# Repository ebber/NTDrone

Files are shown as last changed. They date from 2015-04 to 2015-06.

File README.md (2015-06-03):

# NTDrone
NT Drone DE
This is code to stabilize and control a drone.
3D printing design files coming soon!

Connections:
Pin	Connect to
2	MPU Interupt Pin
6	Motor C Signal Cable
9	Motor D Signal Cable
10	Motor A Signal Cable
11	Motor B Signal Cable
13	LED (blinks error codes)

A4	MPU SDA
A5 	MPU SCA

Using:
Motors/ESC: BEC ESC 10A
input voltage: {6, 7.5, 9, 12 (short periods of time)}

low signal: 900 uS
High signal: 2000uS

Arming sequence:
unneeded 

/*
Previous
Motors/ESC: HobbyKing RedBrick ESC 10A
input voltage: {6, 7.5, 9, 12 (short periods of time)}

low signal: 1000 uS
High signal: 2000uS

Arming sequence:
1000uS
delay(500);
2000uS
//armed
*/

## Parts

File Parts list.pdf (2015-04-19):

| Parts | weight (g) | cost | quantity | total part cost | total part weight (g | overall drone cost | total weight (g)
Motor | 2205C 1400Kv Brushless motor (http://hobbyking.com/hobbyking/store/__7520__2205C_1400Kv_Brushless_motor.html) | 28.00 | $11.75 | 4 | $47.00 | 112.00 | $235.19 | 1,198.43
Propellers | APC style propeller 10x5-E (http://www.hobbyking.com/hobbyking/store/__5440__APC_style_propeller_10x5_E.html) | 35.00 | $0.75 | 4 | $3.00 | 140.00
Speed Controler | HobbyKing Red Brick 10A ESC (http://hobbyking.com/hobbyking/store/__18002__HobbyKing_Red_Brick_10A_ESC.html) | 18.00 | $6.55 | 4 | $26.20 | 72.00

Sensors
acceleramoter | MPU 6050 (http://www.gearbest.com/development-boards/pp_22492.html?currency=USD) | 1.10 | $7.68 | 1 | $7.68 | 1.10
Battery | Turnigy 2200mAh 3S 20C Lipo Pack | 188.00 | $8.76 | 1 | $8.76 | 188.00
Power Distributer | Hobby King Quadcopter distributer (http://hobbyking.com/hobbyking/store/__28255__Hobby_King_Quadcopter_Power_Distribution_Board_USA_Warehouse_.html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) | 27.30 | $4.19 | 1 | | 27.30
ardunio boards | Arduino Uno | 25.00 | $22.63 | 1 | $22.63 | 25.00

Shields
Wireless - XBee | XBee 1mW Trace Antenna - Series 1 (802.15.4) (https://www.sparkfun.com/products/11215) | 5.00 | $24.95 | 1 | $24.95 | 5.00
XBee Shield | XBEE Shield | 37.00 | $10.00 | 1 | $10.00 | 37.00
Bluetooth | SparkFun Bluetooth Mate Gold (https://www.sparkfun.com/products/12580) | | $34.95 | 0 | $0.00

misc.
| 3.5mm bullet male connectors (10pc) (http://www.amazon.com/gp/product/B00J80EP8G/ref=oh_aui_detailpage_o01_s00?ie=UTF8&psc=1) | | 8 | $9.95
| USB B to A (for power) | $5.09 | 1 | $5.09
Airframe | bowel design | 591.03 | 1 | 591.03

Remote Control
Wireless - XBee | XBee 1mW Trace Antenna - Series 1 (802.15.4) (https://www.sparkfun.com/products/11215) | 5.00 | $24.95 | 1 | $24.95
XBee Shield | XBEE Shield | 37.00 | $10.00 | 1 | $10.00
ardunio boards | Arduino Uno | 25.00 | $22.63 | 1 | $22.63
Charger: | Turnigy E3 Compact 2S/3S Lipo Charger 100-240v (http://hobbyking.com/hobbyking/store/__49338__Turnigy_E3_Compact_2S_3S_Lipo_Charger_100_240v_US_Plug_.html) | 0.00 | $12.35 | 1 | $12.35

Parts | weight (g) | cost | quantity | total part cost | total part weight (g | overall drone cost | total weight (g)

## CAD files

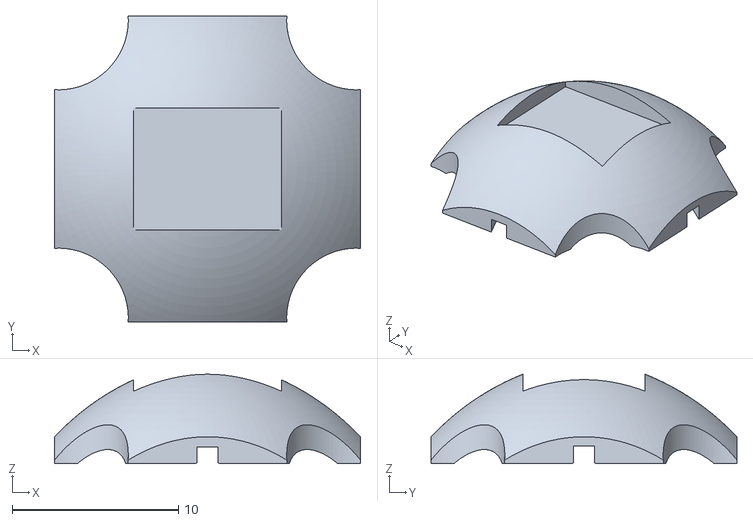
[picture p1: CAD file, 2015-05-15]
3D part files/droneTopCap.stl
18.4 x 18.4 x 5.39

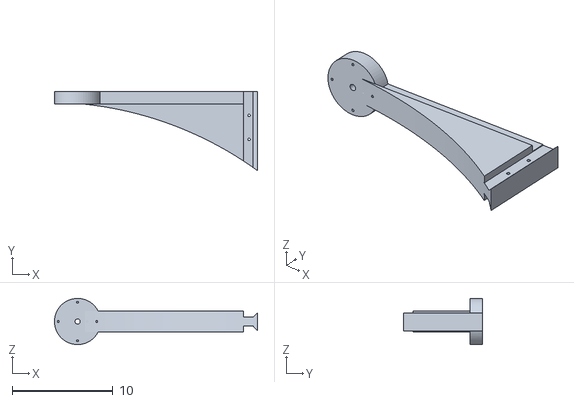
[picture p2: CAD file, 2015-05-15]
3D part files/droneArmV2.stl
20.1 x 7.85 x 4.57

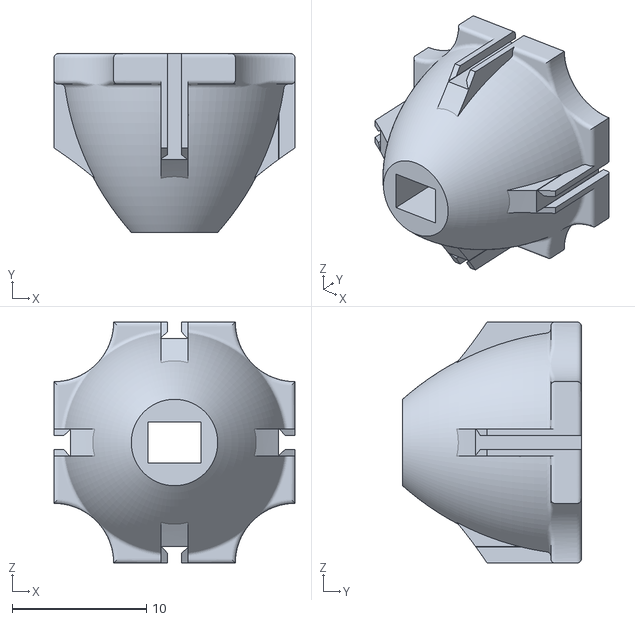
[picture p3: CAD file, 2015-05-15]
3D part files/droneBody.stl
18.0 x 13.3 x 18.0

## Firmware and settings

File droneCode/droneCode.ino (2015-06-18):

#include <Servo.h>
#include <EEPROM.h>


// I2Cdev and MPU6050 must be installed as libraries, or else the .cpp/.h files
// for both classes must be in the include path of your project
#include "I2Cdev.h"

#include "MPU6050_6Axis_MotionApps20.h"
//#include "MPU6050.h" // not necessary if using MotionApps include file

// Arduino Wire library is required if I2Cdev I2CDEV_ARDUINO_WIRE implementation
// is used in I2Cdev.h
#if I2CDEV_IMPLEMENTATION == I2CDEV_ARDUINO_WIRE
    #include "Wire.h"
#endif




// ================================================================
// ===                        Switches                          ===
// ================================================================
//#define OUTPUT_READABLE_YAWPITCHROLL
//#define VERBOSE_SERIAL
//#define OUTPUT_YPR_DIFERENCE
#define MOTOR_SPEEDS
//#define MOTOR_SPEEDS1  //mSpeed \t ypr-targetYPR
//#define DEBUG_PD
//#define CALIBRATE


// ================================================================
// ===                      Description                       ===
// ================================================================
//Purpose of this sketch is to rotate a single DC motor at a constant speed
//then, have it speed up/slow down bassed on accl data


// ================================================================
// ===                      wiring                       ===
// ================================================================
//On the H-Bridge, tie the motor1Pin (2 on breadboard) to high and motor2Pin (7 on breadboard) to Low
//SDA is A4
//SCA is A5
const int mpuInteruptPin = 2;

const int motor0Pin = 10; //A
const int motor1Pin = 11; //B
const int motor2Pin = 6; //C
const int motor3Pin = 9; //D





#define LED_PIN 13 // (on board LED)
bool blinkState = false;


// ================================================================
// ===                      Error Codes                       ===
// ================================================================
/*
{1,1}      Failed to initialize MPU
{1,1,1} failed to initialize DMP

*/


// ================================================================
// ===                      Constants                           ===
// ================================================================
const int minThorttle = 900; //min throttle
const int maxThorttle = 2000; //max throttle

int mYPR[4][3];

const byte pastPoints = 6;
//theres an array thats float d[pastPoints][pastPoints]; grows by the square

const int maxSerialInputLength=15;  //not enforced in code, will silently overflow TODO: fix

const int armSpeed = 700;

const int hoverSpeed = 1450; //random untested value - should be where drone hovers
const int launchSpeed = 1550; //iffy tested exact testing needed -experimentally detirmed to be around here

const int minAcclValue = 0;  //experimentally detirmined
const int maxAcclValue = 100; //experimentally detirmened

const int maxYaw = 180;  
const int minYaw = -180;  

const int minPitch = -60; //TODO: find real Values
const int maxPitch = 60; //TODO: find real Values

const int minRoll = -70; //TODO: find real Values
const int maxRoll = 70; //TODO: find real Values


//TODO1:Find true value
const float PCorrectionMod[3] = {0.1, 1.0, 1.0}; //stabilization modifier (ie correction factor multiplied by this value), based on instantaenous ypr
const float DCorrectionMod[3] = {0.0, 1.0, 1.0};  //take the derivitive of ypr, this is weighting

//for test
float pCorrectionModMultiplier=1.2;
float dCorrectionModMultiplier=0.5;

const float calibrationPercision = 0.1;  //must be positive

/*
Your offsets:  -4592 -537  700 -1214 -18 0
-4550 -523  753 -1269 -23 -2
-4548 -526  751 -1267 -22 -2



Data is printed as: acelX acelY acelZ giroX giroY giroZ

*/





// class default I2C address is 0x68
// specific I2C addresses may be passed as a parameter here
// AD0 low = 0x68 (default for SparkFun breakout and InvenSense evaluation board)
// AD0 high = 0x69
MPU6050 mpu;
//MPU6050 mpu(0x69); // <-- use for AD0 high



// ================================================================
// ===                        EEPROM Addresses                  ===
// ================================================================
const int stdYawAddr = 0;
const int stdPitchAddr = 4;
const int stdRollAddr = 8;

// MPU control/status vars
bool dmpReady = false;  // set true if DMP init was successful
uint8_t mpuIntStatus;   // holds actual interrupt status byte from MPU
uint8_t devStatus;      // return status after each device operation (0 = success, !0 = error)
uint16_t packetSize;    // expected DMP packet size (default is 42 bytes)
uint16_t fifoCount;     // count of all bytes currently in FIFO
uint8_t fifoBuffer[64]; // FIFO storage buffer

// orientation/motion vars
Quaternion q;           // [w, x, y, z]         quaternion container
VectorInt16 aa;         // [x, y, z]            accel sensor measurements
VectorInt16 aaReal;     // [x, y, z]            gravity-free accel sensor measurements
VectorInt16 aaWorld;    // [x, y, z]            world-frame accel sensor measurements
VectorFloat gravity;    // [x, y, z]            gravity vector
float euler[3];         // [psi, theta, phi]    Euler angle container
float ypr[3];           // [yaw, pitch, roll]   yaw/pitch/roll container and gravity vector
float spYPR[3];       //base values when its flat, the SP
float flatYPR[3] = {-100.97,  0.20,  -0.18}; //put in EEPROM

float YPRerr[3][pastPoints];   //
float adjYPRerr[3];


bool newData = false;

String serialData;
bool newSerialData=false;

int throttle=700; //goes from 900 to 2000


Servo motor[4];
float mSpeed[4];

// ================================================================
// ===               INTERRUPT DETECTION ROUTINE                ===
// ================================================================

volatile bool mpuInterrupt = false;     // indicates whether MPU interrupt pin has gone high
void dmpDataReady() {
    mpuInterrupt = true;
}


void setup() { 
  //stupid arduino won't initialize 2D arrays
  //set motor multipliers (how a change efects motor speed). 
  int buffer[4][3] = { { 1, -1,  1}, 
                       {-1,  1,  1},
                       {-1,  1, -1},  
                       { 1, -1, -1}  }; 
           
           //fill array
    for (int x=0; x<4; x++){
     for (int y=0; y<3; y++){
       mYPR[x][y] = buffer[x][y];
     }
    }
        
        
  //actualy setup()
  serialData.reserve(maxSerialInputLength);
  Serial.begin(9600);
  setUpMPU();
  
  
  motor[0].attach(motor0Pin);    // attached to pin 
  motor[1].attach(motor1Pin);    // attached to pin 
  motor[2].attach(motor2Pin);    // attached to pin 
  motor[3].attach(motor3Pin);    // attached to pin 

  // configure LED for output
  pinMode(LED_PIN, OUTPUT);
  

  //9600 is magical. Havent tested to see if any other baud rate are not magical
  
     for(int i=0; i<4;i++) {
      motor[i].writeMicroseconds(armSpeed); //low throtle
   } 
   
   #ifdef VERBOSE_SERIAL
      Serial.println(F("Calibrating yaw pitch roll"));
   #endif
   #ifdef CALIBRATE
   //calibrate
  calibrateYPR(&flatYPR[0]);
  #else
 
        //EEPROM.get(stdYawAddr, flatYPR[0]);
        EEPROM.get(stdPitchAddr, flatYPR[1]);
        EEPROM.get(stdRollAddr, flatYPR[2]);
        getYawPitchRoll(&ypr[0]);
        flatYPR[0]=ypr[0]; //have updataed orientation
        Serial.print(F("Getting old target"));
 
  #endif

  //our target is flat
  for(int i=0; i<3;i++) {
    spYPR[i]=flatYPR[i];
  }

  
    for(int i=0; i<4;i++) {
      motor[i].writeMicroseconds(armSpeed); //low throtle
   } 
  
    // wait for ready
    Serial.println(millis()/1000.);
    Serial.println(F("Press any key to begin: "));
    digitalWrite(LED_PIN,HIGH);
    while (Serial.available() && Serial.read()); // empty buffer
    while (!Serial.available());                 // wait for data
    while (Serial.available() && Serial.read()); // empty buffer again  
    Serial.println(F("Begginiing"));
    spYPR[0]=ypr[0];
  //fill history
  for(int p=0;p<=pastPoints+3;) {
    
    newData = getYawPitchRoll(&ypr[0]);
    if(newData) {
    //shift data, and map it to -33,33
        for(int j=pastPoints-1; j>0; j--) {
           for(int i=0; i<3; i++) {
            YPRerr[i][j] = YPRerr[i][j-1];
           } 
        }
        
        for(int i=0; i<3; i++) {
           YPRerr[i][0] = ypr[i]-spYPR[i];
        }
      p++;
      spYPR[0]=ypr[0];
    }
  }    
}
 
 
void loop() {
  
    newData=getYawPitchRoll(&ypr[0]); //fill acceleration array, and return if we got new data
    
    
   
    
    
    if(newSerialData){
      inputHandler();
    }

    if(newData) {
      
      
      //shift data, and map it to -33,33
      for(int j=pastPoints-1; j>0; j--) {
         for(int i=0; i<3; i++) {
          YPRerr[i][j] = YPRerr[i][j-1];
         } 
      }
      
      for(int i=0; i<3; i++) {
         YPRerr[i][0] = ypr[i]-spYPR[i];
      }
      


      //put yaw through PD
      float axis[pastPoints];
      //no need to mess with yaw constants
      for(int i=0;i<1;i++) {
        //fill axis with all past yaws or pitches or rolls
        for (int j=0; j<pastPoints;j++) {
           axis[j] = YPRerr[i][j];
        }

        adjYPRerr[i]= getPComponent(YPRerr[i][0], PCorrectionMod[i] ) + getDComponent(&axis[0],i,pastPoints,  DCorrectionMod[i]);
      }
      //deal with pitch and roll
      for(int i=1;i<3;i++) {
        //fill axis with all past yaws or pitches or rolls
        for (int j=0; j<pastPoints;j++) {
           axis[j] = YPRerr[i][j];
        }

        adjYPRerr[i]= getPComponent(YPRerr[i][0], PCorrectionMod[i] * pCorrectionModMultiplier) + getDComponent(&axis[0],i,pastPoints,  DCorrectionMod[i]*dCorrectionModMultiplier);
      }


      mapYPR(&adjYPRerr[0]);


      
   for (int k=0; k<4;k++) {
      mSpeed[k] = combineYPR(adjYPRerr[0],  adjYPRerr[1], adjYPRerr[2],k); //from instantaneous
    }
    
    
    noInterrupts();
    spinRotor(motor[0], mSpeed[0]); //spin rotor A
    spinRotor(motor[1], mSpeed[1]); //spin rotor B
    spinRotor(motor[2], mSpeed[2]); //spin rotor C
    spinRotor(motor[3], mSpeed[3]);  //spin rotor D
    
     #ifdef OUTPUT_YPR_DIFERENCE
       for(int i=0;i<3; i++) {
         Serial.print(ypr[i]-spYPR[i]);
         Serial.print("\t");
       }   
       
    #endif
    
    #ifdef MOTOR_SPEEDS1
    
       for(int i=1;i<2; i++) {
         Serial.print((int) mSpeed[i]);
         Serial.print("\t");
       }  
       
       for(int i=2;i<3; i++) {
         Serial.print(ypr[i]-spYPR[i]);
         Serial.print("\t");
       }  
        
       
      Serial.print("\n");
    #endif
   
   #ifdef MOTOR_SPEEDS
    Serial.print(serialData);
    Serial.print("\t");
    Serial.println();
   #endif 
     #ifdef OUTPUT_YPR_DIFERENCE
    Serial.println();
   #endif 

   #ifdef DEBUG_PD
    Serial.print("\n");
   #endif 
 
    interrupts();
    }
}


//Run after loop()
void serialEvent() {
  while (Serial.available() ) {
    // get the new byte:
    char inChar = (char) Serial.read(); 

    if(';'== inChar) {
      newSerialData = true;
      break;
    } else if ('`' == inChar) {
        serialData="";
    } else {
      // add it to the inputString:
      serialData += inChar;
    }
  }
}

void inputHandler() {
  String input=getSerialData(); //GOES FROM 90 TO 200
      
      if(input[0] == 'p') { //its not an int
        
        pCorrectionModMultiplier = ( (String) input[1]).toFloat();
        Serial.println(pCorrectionModMultiplier);
        
      } else if(input[0] == 'd') { //its not an int
        
        dCorrectionModMultiplier = ( (String) input[1]).toFloat();
        Serial.println(dCorrectionModMultiplier);
        
      } else if(input[0] == 'o') { //its not an int
        
        EEPROM.get(stdYawAddr, spYPR[0]);
        EEPROM.get(stdPitchAddr, spYPR[1]);
        EEPROM.get(stdRollAddr, spYPR[2]);
        Serial.print(F("Getting old target"));
        for(int i=0; i<3;i++) {
            Serial.print(spYPR[i]);
            Serial.print("\t");
          }
        
      } else if(input[0] == 'c') { //its not an int
        
        //calibrate
      
          calibrateYPR(&spYPR[0]);
          Serial.println(F("Press any key to begin: "));
          while (Serial.available() && Serial.read()); // empty buffer
          while (!Serial.available());                 // wait for data
          while (Serial.available() && Serial.read()); // empty buffer again
          throttle=minThorttle;
          /*  
          EEPROM.put(stdYawAddr, spYPR[0]);
          EEPROM.put(stdPitchAddr, spYPR[1]);
          EEPROM.put(stdRollAddr, spYPR[2]);
          */
          for(int i=0; i<3;i++) {
            Serial.print(spYPR[i]);
            Serial.print("\t");
          }
          Serial.println();
      } else if('k' == input[0]) {
        
        
      } else if (0 != input.toInt() ) {
        throttle= input.toInt()*10;
        Serial.println(throttle);
        
        if (throttle <= 400) {
          //do nothing, probably a mistaye
        } else if (throttle > 2000) {
          //shit no man
          throttle=700;
        }
      } else {
        Serial.println(input);
      }
}

//takes up to 15 chars
String getSerialData() {
  String data = serialData;
  serialData="";
  newSerialData=false;
  return data;
  
}




float getPComponent(float angle, float kP) {
  angle = angle* kP;
  #ifdef DEBUG_PD
    Serial.print(angle);
    Serial.print("\t");
  #endif
  return angle;
}

//old speed is an array of speeds where [0] is most current and [numOfPoints-1] is oldest
//predictAhead predicts how many points ahead there are
//TODO: make it so if we have extra points in our history, get a better taylor series
float getDComponent(float* oldValues, int axis, int numOfPoints, float kD) {
  // Taylor Series slope
  

     //get the derivatives 
     float d[numOfPoints][numOfPoints];
    //fill the base
    for(int i=0;i<numOfPoints-1;i++) {
     d[0][i]=oldValues[i]; 
    }
    
    for (int i=1;i<numOfPoints;i++) {
      for(int j=0; j<numOfPoints-i; j++) {
        d[i][j]=d[i-1][j]-d[i-1][j+1]; //technically divided by 1 
      }
    }

  float slope = d[1][0];
  for(int i=2; i<numOfPoints-1 ;i++) {
   slope = slope + d[i][0] /( (float) factorial(i) ); 
  }
  
  //float slope = oldValues[1]-oldValues[0];
 float adjSlope=slope*abs(slope)*kD;  //make the sloping bits steeper
  #ifdef DEBUG_PD

    Serial.print(adjSlope);
    Serial.print("\t");
  #endif
  return adjSlope;
  
}


int factorial(int n) {
 if(n>2) {
  return n*factorial(n-1);
 } else {
   return n;
 }
}

//take the (pitch actual - pitch desired) and the (roll actual - roll desired), return speed to change
float combineYPR(float yaw, float pitch, float roll, int motor) {
  
  float cor = (yaw*mYPR[motor][0] + mYPR[motor][1]*pitch + mYPR[motor][2]*roll);

  return cor;
  
}

void mapYPR(float* YPR) {
    //adjust values to -10 to 10 (so total is -30 or 30)
   //yaw
  YPR[0] = mapFloat(YPR[0], minYaw, maxYaw, -33.0, 33.0); 
  //pitch
  YPR[1] = mapFloat(YPR[1], minPitch, maxPitch, -33.0, 33.0);
 //roll 
  YPR[2] = mapFloat(YPR[2], minRoll, maxRoll, -33.0, 33.0);
}


 
// speed change is number, give max and min to make it releative, controls motorA
int spinRotor(Servo motor, float speedChange) {
  int spedeSent = ( (int) speedChange )+throttle;
  
  #ifdef MOTOR_SPEEDS
    Serial.print(spedeSent);
    Serial.print("\t");
  #endif
  
  motor.writeMicroseconds(spedeSent);
  return spedeSent;
}


void calibrateYPR(float* stdYPR) {
  if(throttle>900) {
    Serial.println(F("Cannot calibrate midflight"));
    return; 
  }
   //kill the motors
   for(int i=0; i<4;i++) {
      motor[i].writeMicroseconds(minThorttle); //low throtle
   } 
  Serial.println("Calibrating");
  bool calibrated=false;
  int trials;
  do{
      trials=16;
     do {
       filStdYPR(&stdYPR[0]);
       delay(100);
       trials=trials/2;
     } while( testStdYPR(&stdYPR[0],trials) && trials > 4 );
   calibrated = trials <= 4;
   }while(!calibrated);
   
}

bool testStdYPR(float *YPR, int trials) {
  //just to make sure its not crazy
  if( abs(YPR[0]+YPR[1]+YPR[2]) > abs(maxYaw+maxPitch+maxRoll)) {
    Serial.println("Crazy!");
    return false;
  }
      
  int trial = trials;
  
    float yDif=0;
    float pDif=0;
    float rDif=0;
    
     while(trial>0) {

     while( !getYawPitchRoll(&ypr[0]) ){delay(10);} //fill acceleration array with a new packet
       #ifdef OUTPUT_YPR_DIFERENCE
         for(int i=0;i<3; i++) {
           Serial.print(ypr[i]-YPR[i]);
           Serial.print("\t");
         }   
         Serial.println();
      #endif
      delay(200);

       
       yDif=ypr[0]-YPR[0];
       pDif=ypr[1]-YPR[1];
       rDif=ypr[2]-YPR[2];

       
        if( (abs(yDif) < calibrationPercision) &&  (abs(pDif) < calibrationPercision) && (abs(rDif) < calibrationPercision) ) {
         trial--; 
         delay(150); //if 100, it breaks, and ypr[i]-targetYPR[i] diverges signifigantly, then stabilizes at around //think s its because its too close to the speed of the MPU6050

        } else {
          Serial.println(F("OUT OF BOUNDS"));
         return false; //this isnt a good std, break out 
        }
     }
     

     return true;
  
}

void filStdYPR(float *targetYPR) {

  //give blank slate
  targetYPR[0]=0.0;
  targetYPR[1]=0.0;
  targetYPR[2]=0.0;
  
 //average of 20 values, weighted towards the newest values
 
 int i = 0;
 float tempYPR[3];
 while(i<20) {
   //if mpu has signaled its ready or theres a packet waiting
    while(!getYawPitchRoll(&tempYPR[0])) {delay(3);}
    
    if(abs(tempYPR[0]) < 10000.0) { //no overflow. shouldnt be over 10,000.0
      targetYPR[0] = (2.0*targetYPR[0]+tempYPR[0])/3.0;  
    }
    
    if(abs(tempYPR[1]) < 10000.0) { //to stop overflow - shouldnt be over 10,000.0
      targetYPR[1] = (2.0*targetYPR[1]+tempYPR[1])/3.0;  
    } 
    
    if(abs(tempYPR[2]) < 10000.0) { //to stop overflow on the float - shouldnt be over 10,000.0
      targetYPR[2] = (2.0*targetYPR[2]+tempYPR[2])/3.0;  
    } 
    
    i++;  
 }
 return;
}



void errorMPUInitializationFailure() {
  boolean error[2] = {1,1};
  blinkErrorCode(&error[0],2);
  return;
}
void errorDMPInitializationFailure() {
  boolean error[3] = {1,1,1};
  blinkErrorCode(&error[0],3);
  return;
}


void blinkErrorCode(boolean* errorCode, int len) {
  while (true) {
    int i=0;
    while(i<len) {
      digitalWrite(LED_PIN, errorCode[i]==1 ? (HIGH):(LOW));
      delay(500);
      i++; 
      digitalWrite(LED_PIN, LOW);
      delay(200);
    }
    delay(1000);
  }
  return;
}


//0 is yaw, 1 is pitch, 2 is roll
//ypr must be a array size 3
//returns true if new packet, else returns false
bool getYawPitchRoll(float *YPR) {
// if programming failed, don't try to do anything
    if (!dmpReady) return false;

    // if MPU interrupt or extra packet(s) not available, exit function
    if (!mpuInterrupt && fifoCount < packetSize) {
      return false;
    }

    
    mpuInterrupt = false;
    mpuIntStatus = mpu.getIntStatus();

    // get current FIFO count
    fifoCount = mpu.getFIFOCount();

    // check for overflow (this should never happen unless our code is too inefficient)
    if ((mpuIntStatus & 0x10) || fifoCount == 1024) {
        // reset so we can continue cleanly
        mpu.resetFIFO();
        //Serial.println(F("FIFO overflow!"));

    // otherwise, check for DMP data ready interrupt (this should happen frequently)
    } else if (mpuIntStatus & 0x02) {
        // wait for correct available data length, should be a VERY short wait
        while (fifoCount < packetSize) fifoCount = mpu.getFIFOCount();

        // read a packet from FIFO
        mpu.getFIFOBytes(fifoBuffer, packetSize);
        
        // track FIFO count here in case there is > 1 packet available
        // (this lets us immediately read more without waiting for an interrupt)
        fifoCount -= packetSize;


            mpu.dmpGetQuaternion(&q, fifoBuffer);
            mpu.dmpGetGravity(&gravity, &q);
            mpu.dmpGetYawPitchRoll(YPR, &q, &gravity);
            YPR[0]=YPR[0] * 180/M_PI;
            YPR[1]=YPR[1] * 180/M_PI;
            YPR[2]=YPR[2] * 180/M_PI;
            
        #ifdef OUTPUT_READABLE_YAWPITCHROLL
            // display Euler angles in degrees
            

            Serial.print("ypr\t");
            Serial.print(YPR[0]);
            Serial.print("\t");
            Serial.print(YPR[1]);
            Serial.print("\t");
            Serial.println(YPR[2]);
        #endif
    }

    return true;
}
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

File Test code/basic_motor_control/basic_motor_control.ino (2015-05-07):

/*
Coded by Marjan Olesch
Sketch from Insctructables.com
Open source - do what you want with this code!
*/
#include <Servo.h>  


int value = 900; // set values you need to zero
bool pause=false;

const int motor0Pin = 10; //A
const int motor1Pin = 11; //B
const int motor2Pin = 6; //C
const int motor3Pin = 9; //D

Servo motor[4];

void setup() {

  motor[0].attach(motor0Pin);    // attached to pin 
  motor[1].attach(motor1Pin);    // attached to pin 
  motor[2].attach(motor2Pin);    // attached to pin 
  motor[3].attach(motor3Pin);    // attached to pin 
  
      Serial.begin(9600);    // start serial at 9600 baud

  
  

      // wait for ready
    Serial.println(F("Press any key to arm: "));
    while (Serial.available() && Serial.read()); // empty buffer
    while (!Serial.available());                 // wait for data
    while (Serial.available() && Serial.read()); // empty buffer again
    //For redbricks
    //arm(&motor[0]);
    for(int i=0; i<4;i++) {
      motor[i].writeMicroseconds(900); //low throtle
   } 
    
        // wait for ready
    Serial.println(F("Press any key to begin: "));
    while (Serial.available() && Serial.read()); // empty buffer
    while (!Serial.available());                 // wait for data
    while (Serial.available() && Serial.read()); // empty buffer again
 
}

void loop() {

//First connect your ESC WITHOUT Arming. Then Open Serial and follo Instructions
 
   for(int i=0; i<4;i++) {
    motor[i].writeMicroseconds(value);
   } 
   
  if(Serial.available()) {
    int in=Serial.parseInt();
    value = (in>=900 && in <= 2000) ? in:value;    // Parse an Integer from Serial
    pause =! pause;
  }
  
     Serial.println(value);
  
  
  

}
//for redbrick ESCs
void arm(Servo *motor) {
    //begin arming sequence
   for(int i=0; i<4;i++) {
      motor[i].writeMicroseconds(1000); //low throtle
   } 
   
   delay(5000); //5 seconds is overkill, but want to be sure. This must be written after 4 beeps

  
  Serial.begin(9600);    // start serial at 9600 baud
  
   for(int i=0; i<4;i++) {
      motor[i].writeMicroseconds(2000); //high throtle
   } 
   
   delay(50); //let it get up to speed/register but dont let if lift
   
   for(int i=0; i<4;i++) {
      motor[i].writeMicroseconds(1000); //low throtle
   } 
   
   //end arming sequence
  }

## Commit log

2015-03-25 Removed deprecated timing controls
    Removed deprecated timing motor controls
    specifically the functions run_motor
2015-04-17 Added support for brushless motors
    #include <Servo.h>
    void arm(Servo *motor); //arms the 4 motors
    spinRotorX(); now sends a PPR signal instead of PMW, so as to
    cominucate with ESC rather than HBridge
    Minor
    moved #includes to the top
2015-04-19 created a single run motor funtion
2015-05-08 updated power function
2015-05-08 updated constants on max/min throttle
2015-05-15 Now works
    “power” was replaced with throttle
    Due to a problem with Serial.parseInt(); it reads an multiplies by
    10(i.e. input(90) -> throttle=900;)
    Throttle input range is now [90,200]
    balances pitch and roll
    [droneCode.ino]
2015-05-15 commented out red brick ESC code
2015-05-15 added yaw balancing
2015-05-15 correction modifier
    Added a “correction modifier” that the correction factor is multiplied
    be
    currently set to 1
    [droneCode.ino]
2015-05-15 added TODO comment to correction code
    [droneCode.ino]
2015-05-15 Serial.print() elimination
    deleted or moved to switches most Serial.print statements
2015-05-15 added .stl of parts
    [droneArmV2.stl, droneBody.stl, droneTopCap.stl]
2015-05-24 Added good calibration code
2015-05-26 - numbers now recalibrate
    Also fixed yacclOffset
    went from Map() to mapFloat()
    [droneCode.ino]
2015-05-28 worked on finding correction mod
    [droneCode.ino]
2015-05-30 got rid of PID Motor implementation
2015-06-03 untoggled switches
2015-06-03 untoggle switches
2015-06-15 Turned off switches
2015-06-18 Changed yaw d gain to 0 as when it crossed over from 180 to -180 it flipped the fuck out
    [droneCode.ino]
